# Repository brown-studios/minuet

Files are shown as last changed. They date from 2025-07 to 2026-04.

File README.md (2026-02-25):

# Minuet fan controller

Minuet upgrades your [MAXXAIR Maxxfan](https://www.maxxair.com/products/fans/maxxfan-deluxe/) with a brushless DC motor, home automation features, and accessories.

Improve your quality of life in your campervan, RV, trailer, or truck!

* Replace your fan's original motor with a quieter brushless motor. No more cleaning squeaky motor brushes!
* Install Minuet with simple hand tools. You can revert back to the original equipment later if you want.
* Connect your fan to your home automation system if you have one. Works with your original infrared remote control and wired wall controls too.
* Install the light accessory to add a ring of lights to your fan for illumination and ambiance.
* Install the cover sensor accessory to stop the fan and turn off the lights automatically when you attach an insulated vent cover.
* Enjoy a more polished user experience with enhanced thermostat controls and less beeping.
* Customize your fan as you like because the firmware and hardware are open source!
  * Expand the [ESPHome](https://esphome.io/)-based [firmware](https://github.com/brown-studios/minuet-firmware).
  * Connect off-the-shelf I2C environmental sensors and devices to the [QWIIC](https://www.sparkfun.com/qwiic) port.
  * Make your own hardware accessories for the expansion port.
  * Share your work with the community!

This repository contains the Minuet documentation and hardware design files.  You are welcome to modify the Minuet firmware and hardware subject to the [license terms](#notice) and we encourage you to make your own accessories.  We welcome thoughtful contributions.

*Refer to the [Minuet firmware repository](https://github.com/brown-studios/minuet-firmware) for source code.*

## Get to know Minuet

Watch Minuet in action and follow along with how it was made with these videos:

* [Minuet showcase](https://vimeo.com/showcase/11857354)
* [Minuet build log](https://vimeo.com/showcase/11858950)

## Project status

Minuet is in active development.

The latest prototype is feature complete, works well, and is being tested by a few volunteers.

Our next tasks are finalizing the design, working with manufacturers to fabricate kits with everything you will need to upgrade your Maxxfan, and planning for order fulfillment.  We are also investigating the possibility of manufacturing custom brushless fan motors that will fit into the fan housing with fewer adapters.  Please contact us if you would like to contribute your manufacturing experience to this project.

Watch this space for updates on our progress.  We're thrilled by your interest in Minuet and we look forward to offering you a great upgrade for your Maxxfan!

See [project history](./docs/project-history.md) for the story of how we got here.

## Author's note

Hey folks, I'm Jeff!

I started building my campervan in 2023 after some delightful adventures in New Zealand.  Like many of you, I installed a Maxxfan in my campervan because it was the most popular fan for van builders.  It worked well for a while but less than a year after I installed it, the fan started making some awful squeaking noises.  I tried the usual advice: clean the motor brushes, replace the bearings, run the motor on high for a day, and nothing helped for long.  I tried to ignore the problem.

When the winter rainy season arrived and interrupted my van build, I started the squeaking fan again.  I had already started designing a circuit board to synchronize the Maxxfan with my home automation system and I found it tedious to work around the existing logic of the Maxxfan circuit board.  It occurred to me that it might be easier to design my own controller from scratch... and then I could use a brushless fan motor and solve my fan squeaking problem too!

So here we are.  I've made several prototypes, enjoyed the quiet, added quality of life features, made some friends, and learned a lot along the way.  I'm satisfied with how Minuet has improved my comfort and I hope you'll like it too.

## Getting started

Read these guides to learn how to build, install, and use Minuet and its accessories.

1. [Hardware guide](docs/hardware-guide.md): How to build Minuet hardware.
1. [Installation guide](docs/installation-guide.md): How to install Minuet into your Maxxfan.
1. [User guide](docs/user-guide.md): How to use Minuet.

Good luck and enjoy your fan!

## Compatibility

Minuet is anticipated to be *compatible* with the following Maxxfan models.  Some models have yet to be specifically tested and are shown as unverified in the table.

| Compatible model | Lid type | Lid color | Temperature sensor | Rain sensor | Infrared receiver | Verified |
| --- | --- | --- | --- | --- | --- | --- |
| Maxxfan Deluxe 7500K | rain cover | smoke | yes | no | yes | yes |
| Maxxfan Deluxe 7000K | rain cover | white | yes | no | yes | no |
| Maxxfan Deluxe 6200K | rain cover | smoke | yes | no | no † | no |
| Maxxfan Deluxe 5100K | rain cover | white | yes | no | no † | no |
| Maxxfan Plus 4500K‡ | low profile | smoke | yes | yes | yes | yes |

†: When you install Minuet in a Maxxfan whose keypad does not have a window for an infrared receiver, you will be unable to use Minuet's infrared remote control features. (It may be possible to replace or punch a hole through the keypad to make a window for the infrared receiver and use its features.)

‡: The Maxxfan Plus 4500K lid takes longer to open and close so the firmware must be modified to account for the extra duration as of Minuet v3.0.  This difference will be resolved by improving end-of-travel detection.

Minuet is *not compatible* with the following Maxxfan models.

| Incompatible models | Reason |
| --- | --- |
| Maxxfan Deluxe 5101K, 6201K, 7001K, 7501K, 8001K, 8501K | exhaust only keypad (no in/out button) |
| Maxxfan Deluxe 5301K, 6401K | 4 speed keypad (different buttons) |
| Maxxfan Plus 4000K, 4002K, 4050K | manual lift |
| Maxxfan 4301K, 4401K, 4501K | manual lift |
| Maxxfan Low Profile, Mini, Dome | different electronics |

## Notice

The Minuet software, documentation, design, and all copyright protected artifacts are released under the terms of the [MIT license](LICENSE).

The Minuet hardware is released under the terms of the [CERN-OHL-W license](hardware/LICENSE).

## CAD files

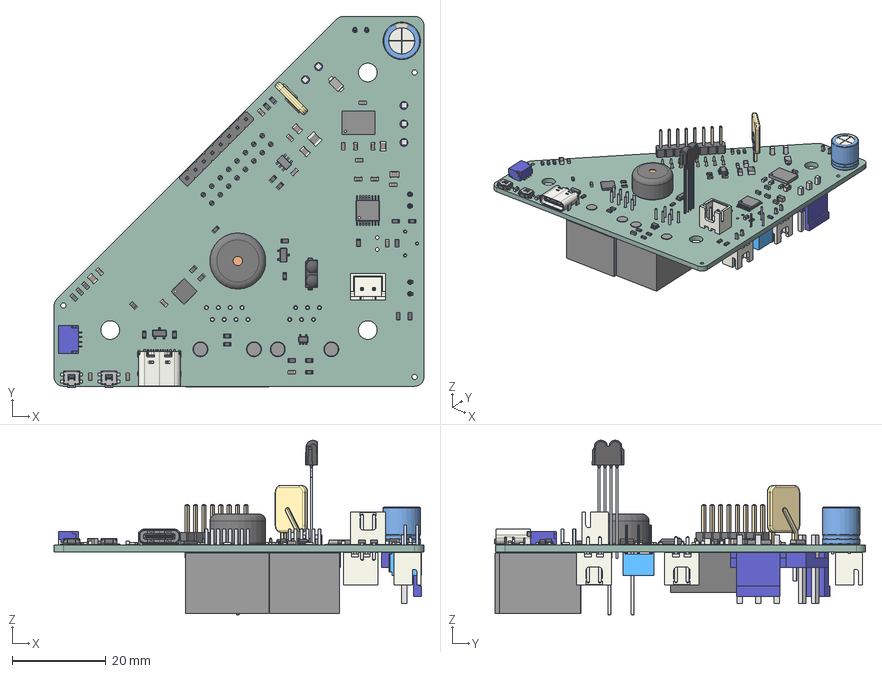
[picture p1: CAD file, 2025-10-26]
hardware/minuet/v4/minuet.step
79.0 x 79.3 x 37.3 mm
C_0805_2012Metric x 5
L_1008_2520Metric
D_SMF
R_0603_1608Metric x 26
C_0603_1608Metric x 17
TPS561201
CP_Radial_D8.0mm_P3.50mm
GO-100220.31
GO-100220.1_Rev01
DRV8876PWPR
SOT-23 x 2
SM04B-SRSS-TB
SW_SPST_EVQP7A x 2
SOT-353_SC-70-5
RGEF400
USB_C_Receptacle_GCT_USB4105-xx-A_16P_TopMnt_Horizontal
Texas_RTW_WQFN-24-1EP_4x4mm_P0.5mm_EP2.7x2.7mm
MCF8316D
Buzzer_TDK_PS1240P02BT_D12.2mm_H6.5mm
PinHeader_1x08_P2.54mm_Vertical
JST_XH_B2B-XH-A_1x02_P2.50mm_Vertical x 4
3362P-1-502LF
Lugs x 2
Leads x 2
B2P-VH-B
PinSocket_2x08_P2.54mm_Vertical
B3P-VH-B
minuet_PCB

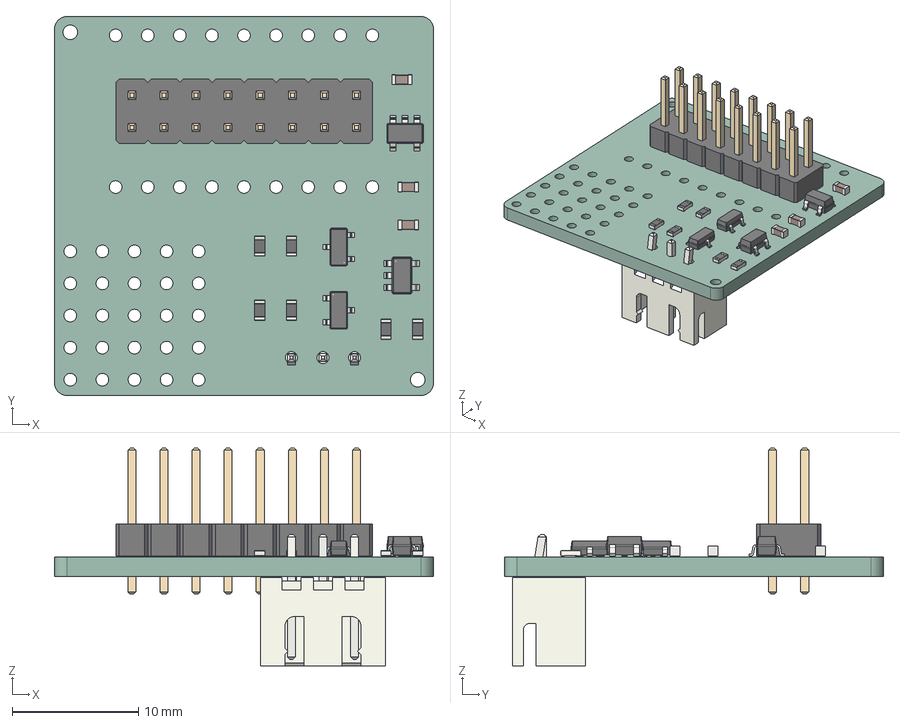
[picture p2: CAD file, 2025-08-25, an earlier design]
hardware/light/v3/light.step
30.0 x 30.0 x 17.2 mm
SOT-23 x 2
PinHeader_2x08_P2.54mm_Vertical
R_0603_1608Metric x 6
SOT-23-5 x 2
C_0603_1608Metric x 3
JST_XH_B3B-XH-A_1x03_P2.50mm_Vertical
light_PCB

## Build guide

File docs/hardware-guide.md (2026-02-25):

# Minuet hardware guide

This guide explains how to build Minuet hardware.

- [Project organization](#project-organization)
- [Main parts](#main-parts)
  - [Fan controller](#fan-controller)
  - [Fan motor and adapters](#fan-motor-and-adapters)
  - [Power cable](#power-cable)
  - [Lid motor cable](#lid-motor-cable)
- [Accessories](#accessories)
  - [Light accessory](#light-accessory)
  - [Cover sensor accessory](#cover-sensor-accessory)
  - [Making your own accessories](#making-your-own-accessories)

> [!TIP]
> Consider buying a Minuet kit when they become available to save yourself time and money.  And read on to learn about the hardware!

# Project organization

## Circuit board designs

The [hardware](../hardware/) folder contains all of the Minuet circuit board designs.

Each circuit board major revision resides in its own subfolder and includes a KiCad project, design document with errata, PDF plot of the schematics, and 3D renderings.  Refer to the `design-and-errata.md` for each circuit board to learn how it's supposed work, how the design has evolved through each minor revision, what was learned from that revision, and workarounds for known issues.

- [Minuet v3 design and errata](../hardware/minuet/v3/design-and-errata.md)
- [Light accessory v3 design and errata](../hardware/light/v3/design-and-errata.md)

## Fabricating circuit boards

Refer to each circuit board's design document for specific fabrication notes.

This repository does not contain fabrication files; you can generate them from the KiCad project in whatever format you need.

The KiCad projects contain part numbers and placement information for the JLCPCB PCBA service.  Use the [Fabrication Toolkit](https://github.com/bennymeg/Fabrication-Toolkit) plugin for KiCad to generate the fabrication files for JLCPCB including the gerber files, bill of materials, and part positions.  Many of the parts in the design were selected to reduce fabrication cost at JLCPCB.  At the time of this writing, the MCF8316D motor driver chip had to be sourced from the global supply chain because was not a regularly stocked item at JLCPCB.

If you're using a different PCBA service, you'll need to select equivalent parts.

Some of the SMT parts have fine pitch QFN pads that are not accessible to a soldering iron.  You may need a solder stencil and reflow equipment to assemble these parts reliably.

You may find it more cost effective to have the factory assemble front-side SMT and through-hole parts and then install the remaining back-side through-hole parts by hand.

## Circuit board design guidelines

Here are a few guidelines to consider when contributing to the Minuet circuit board designs:

- Do not check in fabrication files because they're hard to keep in sync with the design files.
- Include links to datasheets for each chip in the KiCad symbols.
- Prefer two-layer boards to keep the designs accessible for hobbyists.
- Prefer SMT parts no smaller than 0603 and keep the layout somewhat sparse to facilitate hand assembly.
- Place SMT parts on the front side of the board only.
- Place through-hole parts on either side as needed for mechanical reasons.
- Place prominent silk screen labels next to each connector and reference it in the documentation.
- Assign net classes to nets that carry high current.
- Record errata in the design document.

## KiCad resources

To edit the hardware projects, you will need the following:

- KiCad version 9.0 or newer
- KiCad add-ons installed using the Plugin and content manager
  - [Espressif Library](https://github.com/espressif/kicad-libraries): symbols and footprints
  - [JLCPCB Fabrication Toolkit](https://github.com/bennymeg/Fabrication-Toolkit): exports files for manufacturing

# Main parts

## Fan controller

The Minuet fan controller circuit board drives the show.

It is a drop-in replacement for the original Maxxfan circuit board with the original fasteners in the same screw positions and it supports all of the built-in Maxxfan hardware (except the fan motor because that's been replaced by a brushless motor).  Of course, it can do a whole lot more in the same space!

This circuit board has special assembly instructions for the infrared receiver and for adjusting the lid motor current limit trim potentiomer.

Circuit board details: [Minuet v3 design and errata](../hardware/minuet/v3/design-and-errata.md)

Once you've fabricated the circuit board, install the [Minuet firmware](https://github.com/brown-studios/minuet-firmware).

## Fan motor and adapters

Minuet uses a brushless DC motor to drive the fan instead of the original brushed DC motor.

Here's how to choose a fan motor and make adapters to fit the motor to the fan housing.  We recommend choosing a known compatible motor if possible because the process for tuning motors is somewhat challenging.

### Compatible motors

#### StepperOnline 57BYA54-12-01 ([supplier](https://www.omc-stepperonline.com/12v-3000rpm-0-16nm-50w-5-90a-57x57x53-5mm-brushless-dc-motor-57bya54-12-01))

**This is the only motor currently supported out-of-the-box by Minuet.**

- Runs quietly and continuously from about 100 RPM to over 1200 RPM.
- Readily available, compact, and inexpensive.
- Needs a shaft adapter to extend the shaft to reach the fan blade.
- Needs a mount adapter to compensate for the screw hole locations.
- The hall sensors are not needed and are not used by Minuet.

##### Specifications

- Rated voltage: 12 V
- Rated power: 50 W
- Rated current: 5.9 A
- Motor poles: 4
- Sensor type: 3 digital hall sensors with 30° placement
- Shaft diameter: 8 mm
- Shaft length: 21 mm
- Fastener: 4x M4 screws
- Dimensions: 57 mm diameter x 53.5 mm length

##### Wiring chart

- Phase A: fat yellow wire
- Phase B: fat green wire
- Phase C: fat blue wire
- The remaining wires are for the unused hall sensor and can be secured out of the way or cut off

### Bringing up other motors

#### Motor selection guide

Choose a motor that runs quietly at low speed with minimum vibration.  It doesn't need a lot of torque.  For safety, it must be able to operate continously under load without overheating.  Look for motors that are designed for use in appliances (not for skateboards or model airplanes).

The motor must be brushless.  The 3 phases can be wired in either the wye or delta configuration.

The motor should have a datasheet with published specifications so you know what you're getting.

The motor should have a suitable power rating, perhaps somewhere around 50 W, certainly not hundreds of watts.  Bigger is not better.  Big motors have big magnets and they experience significant [cogging torque](https://en.wikipedia.org/wiki/Cogging_torque) when operated at low speeds which results in excessive noise and vibration for a vent fan.

The motor should be designed for operation at a nominal 12 V.  The actual operating voltage will depend on the supply voltage.

The motor should have a minimum current rating of 4 A per phase.  You can use a smaller motor with a lower current rating but it may not be powerful enough to operate the fan at higher speeds.

The motor should not have hall sensors.  It's ok to have them but Minuet v3 does not use them (previous versions of Minuet did).

You are unlikely to find a suitable motor that is a perfect drop-in replacement for the original motor's dimensions.  That's just physics.  Brushless DC motors are generally more efficient than brushed DC motors of equivalent power so they tend to be smaller.  So you will likely need to make adapters to compensate for the different motor body size, mounting hole pattern, shaft diameter, shaft length, and shaft keying.

#### Motor tuning

Before you can operate a new motor with Minuet, you will need to add the motor to a [table in the Minuet firmware](https://github.com/brown-studios/minuet-firmware/blob/main/minuet/fan_driver.h) and tune a large number of parameters for the [MCF8316D field-oriented control motor driver chip](https://www.ti.com/lit/ds/symlink/mcf8316d.pdf).

Those parameters include:

- Number of poles
- Winding resistance
- Winding inductance
- Back-EMF constant
- Speed control loop terms
- Current limit
- Open loop and closed loop acceleration
- Initial position detection
- Operating speed table

Some of these parameters can be measured or estimated directly by the motor driver chip using the built-in Motor Parameter Extraction Tool.  Other parameters require experimentation to determine optimal values for reliable operation.  It is helpful to have a TI MCF8316D-EVM development board and the TI Motor Studio software.

If the motor spins the wrong direction (e.g. intake when it should be exhaust), swap any two motor phases and record that in your wiring chart.

Explaining the process of motor tuning in detail is beyond the scope of this guide.

### Motor wiring

Here's how to attach a connector to your fan motor if it doesn't already have one that's compatible with Minuet.

##### Supplies

- [JST VH series wire-to-board connectors](https://www.jst.com/products/crimp-style-connectors-wire-to-board-type/vh-connector/)
  - 1x JST VH series VHR-3M housing
  - 3x JST VH series SVH-41T-P1.1 contacts plus a few spares just in case
  - If your wires are too short (see instructions)
    - 18 AWG wire, heat shrink tubing, and soldering supplies
  - A crimping tool

##### Instructions

- Locate the wiring chart for your motor and note the color of the A, B, and C phases.
- Measure your wires.  The wires need to be about 16-20" or 40-50 cm long to comfortably reach from the motor to the circuit board within the fan housing.  If your wires are too short then you can solder on some additional 18 AWG wire.
- Strip the wires back about 1.5 mm.
- Crimp the pins onto each wire.
- Note the numbers or index markings on the side of the connector housings to determine the pin order.
- Assemble the 3-pin motor connector as follows:
  - pin 1: Phase A
  - pin 2: Phase B
  - pin 3: Phase C
- Give the wires a gentle tug to ensure they have been fully seated and latched into the housing.

### Motor shaft adapter

The original fan motor has a 40 mm long, 8 mm diameter D-shaped shaft, with a flat face on one side where the fan blade attaches with a 26 mm deep hub.  Your motor's shaft is probably different so you will need a shaft adapter to achieve the necessary length and diameter.

Here are some ways to assemble a suitable shaft adapter.

#### Rigid coupler and dowel pin shaft adapter

This adapter consists of two parts, a rigid coupler to match the shaft diameter and an 8 mm dowel pin to extend its length to fit the fan blade.

TODO: Add a photo

##### Supplies

- Rigid coupler.  The inner diameter of one end of the coupler must match the diameter of your motor shaft and the other end must be 8 mm to match the dowel pin.
  - [5 mm to 8 mm inner diameter, 22 mm long stainless steel coupler](https://www.amazon.com/gp/product/B07P82D36N/)
  - [8 mm to 8 mm inner diameter, 22 mm long stainless steel coupler](https://www.amazon.com/gp/product/B07P5YZKY5/)
- Dowel pin.  The exposed length of the dowel pin must be at least 26 mm for the fan blade plus enough to insert into the shaft coupler.  A dowel pin with 40 mm overall length works well with the couplers linked above.
  - [8 mm x 40 mm stainless steel dowel pin](https://www.amazon.com/gp/product/B07Z6GC2TR/)

##### Instructions

1. Optional: File a shallow flat face into one end of the dowel pin about 15 mm long.  The flat face helps to prevent the fan blade's grub screw from slipping on the shaft although it doesn't seem to make much difference so you can skip this step.
1. Seat the 8 mm dowel pin up to the midpoint of the coupler such that about 26 to 30 mm of the shaft (flattened end) sticks out.  Gently tighten the coupler's grub screws onto the dowel pin.
1. Insert the coupler onto the motor shaft.  Gently tighten the coupler's grub screws onto the dowel pin.

#### 3D printed shaft adapter

Here's a [model for a 3D printed shaft adapter](https://cad.onshape.com/documents/c87749ce3cf87a164617aa11/w/1134a70d634f5c16dbb7ae0d/e/bb8abe1ffa8084825e8f7efa).  You can configure the model for whatever motor shaft diameter you need.  Attach the adapter to the motor shaft with a pair of M4 grub screws.

**Safety notice**: The shaft adapter experiences significant torque while running the fan so there's a risk it might break or slip off the shaft and hurt someone.  Consider making a shaft adapter from more robust materials.  Please be careful!

TODO: Add a photo

### Motor mount

You will need a mount to securely attach your new fan motor to the Maxxfan's housing which was originally designed for a motor with different dimensions.

The mount has three essential features:

- Two M5 screws spaced 50 mm apart across the diameter of the motor for mounting the motor to the housing, just like the original motor.
- Screw holes for fastening the new motor to the mount.
- Spacers to backset the new motor from the housing to compensate for the excess length of the shaft adapter so the fan blade fits properly.  Without them, the fan blade will stick out too far to fit behind the insect screen.

Here are some ways to assemble a suitable mount.

#### 3D printed mount

Here's a [configurable model](https://cad.onshape.com/documents/11f07c0bb608e7010778ac35/w/a82f75dceda39e564795dbd4/e/9979bb27f5cf3d9f46ddfa29) that you can use as a starting point.  It has integrated spacers and stiffening ribs to backset the motor so the shaft sticks out just the right amount for the fan blade to attach.

Use a strong plastic with good heat and UV resistance such as PETG.

TODO: Add a photo

##### Supplies

- 2x M5 x 14 mm cap screws (a little longer is ok) and washers
- Screws for your motor and shaft adapter combination
  - For 57BYA54 with a rigid coupler and dowel pin shaft adapter, use 4x M4 x 22 mm socket head cap screws and washers

##### Instructions

1. Tap the M5 screw holes into the plate.
1. Screw the M5 screws through the mount from the side on which the motor is installed.  Tighten only until snug to avoid stripping the plastic threads.  Do not use threadlocker.
1. Screw the motor to the plate.  Add a washer on each screw between the screw head and the plate.

### Wire passage cover

The notch in the original wire passage cover is too small to fit over the motor wires.

You can modify the original wire passage cover to fit, make a new cover, or omit the cover (increasing the risk of water intrusion).

#### 3D printed cover

Here's a [configurable model](https://cad.onshape.com/documents/c87749ce3cf87a164617aa11/w/1134a70d634f5c16dbb7ae0d/e/c150dd1f03cfafd0dbefc852) that you can use as a starting point.

Use a strong plastic with good heat and UV resistance such as PETG.

TODO: Add a photo

## Power cable

The power cable uses a [JST VH series wire-to-board connector](https://www.jst.com/products/crimp-style-connectors-wire-to-board-type/vh-connector/).

- Pin 1 is negative (ground)
- Pin 2 is positive (+12 V DC nominal)

TODO: Add a photo

##### Supplies

- 1x JST VH series VHR-2M housing
- 2x JST VH series SVH-41T-P1.1 contacts plus a few spares just in case
- 18 AWG wire, preferably in distinct colors to help identify positive (red) and negative (black)
- wire crimping tools

##### Instructions

- Cut two pieces of wire long enough to make the connection from the fan housing where the circuit board will be installed to the electrical supply.  About 12" or 30 cm should be plenty.  Alternatively, you can crimp the contacts directly to the electrical supply wire.
- Strip 2 mm off the end of the wire.
- Crimp the JST VH contacts to the wires.
- Insert the contacts into the JST VH housing paying attention to the polarity chart shown above.

## Lid motor cable

This cable adapts the lid motor's [Molex 1625 series wire-to-wire connector](https://www.molex.com/en-us/products/series-chart/1625) to Minuet's [JST XH series wire-to-board connector](https://www.jst.com/products/crimp-style-connectors-wire-to-board-type/xh-connector/).

TODO: Add a photo

##### Supplies

- 1x Molex 1625 series 03061023 (1625-2R3) receptacle
- 2x Molex 1625 series 02061101 contacts plus a few spares just in case
- 1x JST XH series XHP-2 2-pin housing
- 2x JST XH series SXH-001T-P0.6(N) contacts plus a few spares just in case
- 22 AWG 2 conductor ribbon cable
- wire crimping tools

##### Instructions

- Cut a section of ribbon cable approximately 12" or 30 cm long.
- Strip 1.5 mm off from each end of each wire.
- Crimp a Molex 1625 series pin to one of each wire and a JST XH series pin to the other end.
- Insert the pins into their respective housings such that pin 1 of the Molex 1625 series connector connects to pin 1 of the JST XH series connector.  Likewise, pin 2 connects to pin 2.

# Accessories

## Light accessory

The Minuet light accessory lets you attach a light to your fan.  It plugs into the Minuet `EXPANSION` port.

You can use this accessory as a break-out board for your own circuits and it includes a prototyping area for mounting through-hole components.

Circuit board details: [Minuet light accessory v3 design and errata](../hardware/light/v3/design-and-errata.md)

### LED strip

This section section describes how to build an addressable LED strip with a connector that works with Minuet out-of-the-box.  You can use a different LED strip instead but you may need to customize the firmware to interface with it correctly.

TODO: Add a photo

##### Supplies

- 1 meter of [BTF Lighting SK6812 RGBWW, IP65, 60 LEDs/meter, 12 V](https://www.btf-lighting.com/products/dc12v-sk6812-rgbw-led-strip-individual-addressable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) or similar
- 1x JST XH series XHP-3 3-pin housing
- 3x JST XH series SXH-001T-P0.6(N) contacts plus a few spares just in case
- 22 AWG 3 conductor ribbon cable
- wire crimping tools
- heat shrink tubing

##### Instructions

- Cut a section of ribbon cable approximately 12" or 30 cm long.
- Cut a section of 57 pixels from the LED strip.  This is enough to fit around the inner circumference of the fan housing.
- Solder one end of each wire to the `GND`, `DIN`, and `12V` terminals of the LED strip.
- Install a short section of heat shrink tubing over the solder joint.
- Strip 1.5 mm off from the other end of each wire.
- Crimp a JST XH series pin to one end of each wire.
- Insert the pins into the JST XH series housing such that pin 1 connects to `GND`, pin 2 connects to `DIN`, and pin 3 connects to `12V`.

## Cover sensor accessory

The cover sensor accessory detects when you have installed an insulated vent cover and engages the safety lock to turn off the fan and the light.

It's a normally-open reed switch that plugs into the `LOCK` connector.  The reed switch closes the circuit when a magnet on the cover is adjacent to it.

TODO: Add a photo

##### Supplies

- 1x normally-open reed switch with axial leads, such as [this one](https://www.amazon.com/dp/B07YFBQ4HS)
- 1x JST XH series XHP-2 2-pin housing
- 2x JST XH series SXH-001T-P0.6(N) contacts plus a few spares just in case
- 22 AWG 2 conductor ribbon cable
- wire crimping tools
- heat shrink tubing

##### Instructions

- Cut a section of ribbon cable approximately 24-30" or 60-75 cm long.  It needs to be long enough to reach from the fan controller to the fan ceiling flange where it can sense the magnet on the cover.
- Bend one lead of the reed switch over so that both leads point the same direction.
- Solder one end of each wire to each lead of the reed switch.  To keep things tidy, it helps to trim the wire and the leads so they lay flat before soldering.
- Install a section of heat shrink tubing over the reed switch and its leads.
- Strip 1.5 mm off from the other end of each wire.
- Crimp a JST XH series pin to one end of each wire.
- Insert the pins into the JST XH series housing.  The pin order doesn't matter.

## Making your own accessories

Minuet gets better when you take advantage of its place in the middle of your vehicle's roof for accessories.

- Attach many off-the-shelf [QWIIC](https://www.sparkfun.com/qwiic) compatible I2C peripherals to Minuet with just a wire.
- Use the [Light accessory](#light-accessory) as a break-out board for your own circuits and it includes a prototyping area for mounting through-hole components.
- Make your own circuit board that plugs into the `EXPANSION` port.

Refer to the [Minuet v3 design and errata](../hardware/minuet/v3/design-and-errata.md) and schematics for the electrical parameters of these ports.

> [!TIP]
> You will likely need to customize the [Minuet firmware](https://github.com/brown-studios/minuet-firmware) for your accessory.  We recommend consulting the list of [ESPHome components](https://esphome.io/components/) to help choose your peripherals so you won't need to write as much code to get them working.

Here are some ideas of stuff you could build:

- Add a CO₂, temperature, humidity sensor: [scd4x sensor](https://esphome.io/components/sensor/scd4x.html)
- Add a temperature, pressure sensor, humidity, gas sensor: [bmp680 sensor](https://esphome.io/components/sensor/bme680)
- Add a button near the fan to trigger something: [gpio binary sensor](https://esphome.io/components/binary_sensor/gpio)
- Add a relay to do something when the fan is running: [gpio switch](https://esphome.io/components/switch/gpio)
- Detect when humans are present: [dfrobot sen0395](https://esphome.io/components/dfrobot_sen0395)

Consider sharing your new accessory with others! ❤️

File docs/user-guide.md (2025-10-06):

# Minuet user guide

This guide explains how to use Minuet.

- [Main functions](#main-functions)
- [Light accessory functions](#light-accessory-functions)
- [WiFi network](#wifi-network)
- [Automation](#automation)
- [Minuet app (help wanted)](#minuet-app-help-wanted)

# Main functions

You can control most of the fan's functions using the built-in keypad.  Some functions can only be used when you have certain accessories installed or using automation (see related sections).

## Using the built-in keypad and the 6 key wall remote

Minuet supports two different control schemes for the built-in keypad and the 6 key wall remote.  After all, why not improve on the fan controls when you're already replacing its brains!

The [enhanced controls](#enhanced-controls) are enabled by default and make the automatic thermostat easier to use and more capable.

If you prefer, you can enable the [standard controls](#standard-controls) instead to mimic the original Maxxfan controls with some loss of functionality.

### Quick reference

These button combinations vary by control mode.

| Button combination | Enhanced controls | Standard controls (manual mode) | Standard controls (auto mode) |
| --- | --- | --- | --- |
| press `up` | speed up | speed up | thermostat temperature up |
| hold `up` for 1 second | speed maximum | speed maximum | |
| press `down` | speed down | speed down | thermostat temperature down |
| hold `down` for 1 second | speed minimum | speed mimimum | |
| press `in/out` | direction in/out | direction in/out | direction in/out |
| press `on/off` | fan on/off | fan on/off | thermostat disable (return to manual mode) |
| press `open/close` | lid open/close | lid open/close | |
| press `auto` | thermostat enable/disable | thermostat enable (enter auto mode) | thermostat disable (return to manual mode) |
| hold `auto` for 3 seconds | thermostat reset | | thermostat reset |
| hold `auto` and press `up` | thermostat temperature up | | |
| hold `auto` and press `down` | thermostat temperature down | | |
| hold `auto` and press `in/out` | thermostat direction toggle | | |
| hold `auto` and press `on/off` | thermostat function toggle | | |

These button combinations are common to all modes.

| Button combination | Behavior |
| --- | --- |
| press `rain` | rain sensor toggle (only for models with rain sensors) |
| hold `auto` and `up` for 5 seconds | use enhanced controls |
| hold `auto` and `down` for 5 seconds | use standard controls |
| hold `auto` and `open/close` for 5 seconds | keypad indicator toggle |
| hold `on/off` and `in/out` for 5 seconds | manual safety lock toggle |
| hold `on/off` and `down` for 5 seconds | WiFi toggle |
| hold `on/off` and `up` for 5 seconds | power on restore toggle |
| hold `on/off` for 15 seconds | factory reset |

These button combinations are available when you have the corresponding accessory installed.

| Button combination | Light accessory |
| --- | --- |
| hold `in/out` for 1 second | light on/off |
| hold `in/out` for press `up` | brightness up |
| hold `in/out` for press `down` | brightness down |

### Enhanced controls

The enhanced controls let you keep the automatic thermostat enabled while you manually override its behavior for particular situations like when you need extra ventilation for cooking indoors.  The buttons always behave the same way regardless of whether the thermostat is enabled.

While the thermostat is disabled, the `auto` indicator is unlit and the buttons control the fan state similar to the standard controls.

While the thermostat is enabled, the `auto` indicator is lit and the thermostat controls the fan state automatically based on the ambient temperature.  However, if you press a button or send an automation request to change the state of the fan with enhanced controls then your manual settings *override* the behavior of the thermostat.  This behavior differs from the [standard controls](#standard-controls) where such changes are disallowed unless the thermostat is disabled.

While the thermostat is overridden, the `auto` indicator blinks and the buttons control the fan state similar to the standard controls.  The thermostat will remain overridden state by your manual settings until you press `auto` to re-engage the thermostat.

Hold `auto` and press other buttons to modify the thermostat temperature set point, direction, and function with the keypad.  Use the [automation](#automation) interfaces to configure more advanced features of the thermostat.

*To enable the enhanced controls, press and hold `auto` and `up` simultaneously for 5 seconds.  Minuet confirms with three quick tones followed by a long high tone.*

#### Buttons

- Press `up`: increase the fan speed by one
- Hold `up` for 1 second: increase the fan speed to maximum *(bonus)*
- Press `down`: decrease the fan speed by one
- Hold `down` for 1 second: decrease the fan speed to minimum *(bonus)*
- Press `in/out`: toggle the fan direction between air in and air out
- Press `on/off`: toggle the fan off or turn it on at its last selected manual fan speed
- Press `open/close` (`up` and `down` together): toggle the lid open or closed
- Press `auto`: enable the thermostat if it is disabled, re-engage the thermostat if it is overridden, otherwise disable the thermostat
- Hold `auto` for 3 seconds: reset thermostat to default temperature setpoint of 78 °F (approx. 25.5 °C), default direction, and default function, Minuet confirms with a quick turn
- Hold `auto` and press `up`: increase thermostat temperature setpoint by 1 °F (approx. 0.5 °C), Minuet confirms with a quick rising tone
- Hold `auto` and press `down`: decrease thermostat temperature setpoint by 1 °F (approx. 0.5 °C), Minuet confirms with a quick falling tone
- Hold `auto` and press `in/out` one or more times: set the thermostat direction according to the number of presses of `in/out` as indicated in the *thermostat direction* table

  | Thermostat direction | Key presses | Behavior | Confirmation |
  | -------------------- | ----------- | -------- | ------------ |
  | *default* | 1 | use the last selected manual fan direction | two quick tones |
  | *air out* | 2 | exhaust air from the vehicle | quick rising scale |
  | *air in* | 3 | draw air into the vehicle | quick descending scale |

- Hold `auto` and press `on/off` one or more times: set the thermostat function according to the number of presses of `on/off` as indicated in the *thermostat function* table

  | Thermostat function | Key presses | Fan mode | Lid mode | Behavior | Confirmation |
  | ------------------- | ----------- | -------- | -------- | -------- | ------------ |
  | *default* | 1 | fan auto | lid auto | **best for cooling**: automatic fan speed control | long tone, quick tone |
  | *quiet* | 2 | fan quiet | lid open | **best for sleeping**: quieter automatic fan speed control, lid stays open even below the temperature setpoint to provide fresh air and eliminate actuator noises (unless overridden by a safety lock) | long tone, two quick tones |
  | *low* | 3 | fan low | lid auto | **best for energy efficiency**: fan speed at minimum | long tone, three quick tones |
  | *passive* | 4 | fan off | lid auto | **best for passive ventilation**: fan stays off | long tone, four quick tones |

### Standard controls

The standard controls mimic the original Maxxfan controls with a few *bonus* convenience features.

The buttons behave differently depending on whether the fan is in manual or in auto mode.  Check the state of the `auto` indicator light before pressing buttons to avoid surprises.  For example, in manual mode the `up` and `down` buttons control the fan speed whereas in auto mode the `up` and `down` buttons control the thermostat temperature setpoint.

If Minuet receives an automation request to change the fan speed or open/close the lid while auto mode is active with standard controls, it returns to manual mode before performing the requested action.  This behavior differs from the [enhanced controls](#enhanced-controls) where such changes are allowed and override the behavior of the thermostat.

*To enable the standard controls, press and hold `auto` and `down` simultaneously for 5 seconds.  Minuet confirms with three quick tones followed by a long low tone.*

#### Buttons in manual mode (`auto` indicator is unlit)

In manual mode, the up/down buttons control the fan speed and the on/off button toggles the fan on or off.

- Press `up`: increase the fan speed by one
- Hold `up` for 1 second: increase the fan speed to maximum *(bonus)*
- Press `down`: decrease the fan speed by one
- Hold `down` for 1 second: decrease the fan speed to minimum *(bonus)*
- Press `in/out`: toggle the fan direction between air in and air out
- Press `on/off`: toggle the fan off or turn it on at its last configured manual fan speed
- Press `open/close` (`up` and `down` together): toggle the lid open or closed
- Press `auto`: enable the thermostat, enter auto mode

#### Buttons in auto mode (`auto` indicator is lit)

In auto mode, the up/down buttons control the thermostat temperature setpoint, the on/off button exits auto mode, and the thermostat controls the fan speed based on the ambient temperature.  The thermostat will turn the fan on in the direction it last operated in.

- Press `up`: increase thermostat temperature setpoint by 1 °F (approx. 0.5 °C), Minuet confirms with a quick rising tone
- Press `down`: decrease thermostat temperature setpoint by 1 °F (approx. 0.5 °C), Minuet confirms with a quick falling tone
- Press `in/out`: toggle the fan direction between air in and air out
- Press `on/off`: disable the thermostat, return to manual mode
- Press `open/close` (`up` and `down` together): *inoperable in this mode*
- Press `auto`: disable the thermostat, return to manual mode
- Hold `auto` for 3 seconds: reset thermostat to default temperature setpoint of 78 °F (approx. 25.5 °C), Minuet confirms with a quick turn

### Rain sensor (only for models with rain sensors)

Press the `rain sensor` button to toggle the rain sensor on or off.

When the rain sensor is disabled, the LED will turn red to warn that water could enter your vehicle if it rains.

When the rain sensor detects moisture, it turns off the fan, closes the lid, makes the LED flash red, and activates the safety lock feature.  The fan cannot be operated while the safety lock is activated.  Press the `rain sensor` button again to reset the flashing LED and release the rain sensor safety lock.

### Safety lock

The safety lock feature closes the lid and prevents the fan from being operated whenever one or more of the following conditions occur:

| Reason | Condition | How to release |
| --- | --- | --- |
| Battery safety lock | The battery voltage is too low to too high. | Wait for the battery voltage to return to the normal operating range or adjust the low or high battery voltage thresholds. |
| Rain safety lock | The rain sensor is enabled and detected moisture. | Press the `rain sensor` button to reset or turn off the rain sensor. |
| Accessory safety lock | An accessory triggered the `LOCK` signal. | Consult the documentation of your accessories for details. For example, if you have a sensor to detect the presence of an insulated vent cover then remove the cover. |
| Manual safety lock | The [manual safety lock](#manual-safety-lock) is enabled. | Disable the [manual safety lock](#manual-safety-lock). |
| Automation safety lock | The [automation safety lock](#automation-safety-lock) is enabled. | Disable the [automation safety lock](#automation-safety-lock). |

You cannot turn the fan on or open the lid while the safety lock is active.  If you try, Minuet plays three quick tones as a warning and rejects the request.

The safety lock also turns off and inhibits the light accessory.

#### Manual safety lock

Use the manual safety lock to keep the fan off and the lid closed to prevent the fan from operating accidentally or under control of the thermostat.  For example, it can be helpful to keep out dust and wildfire smoke in extreme conditions or perhaps to discourage an inappropriately inquisitive child from turning on the fan.

Hold `on/off` and `in/out` together for 5 seconds to toggle the manual safety lock.  By default, the manual safety lock is disabled.

When the manual safety lock is enabled, Minuet confirms with two quick tones followed by a long high tone.

When the manual safety lock is disabled (default), Minuet confirms with two quick tones followed by a long low tone.

#### Automation safety lock

Use the automation safety lock to develop automations that keep the fan off and the lid closed under software defined conditions.  Unlike [manual safety lock](#manual-safety-lock), the automation safety lock cannot be toggled using the keypad; it can only be toggled by automations.

For example, you could write an automation to enable the automation safety lock while driving (to reduce road noise and fumes) and disable it when parked.

### WiFi mode

Hold `on/off` and `down` together for 5 seconds to toggle WiFi on or off.  By default, WiFi is turned off.

When WiFi is turned on, Minuet confirms with four quick tones followed by a long high tone.

When WiFi is turned off (default), Minuet confirms with four quick tones followed by a long low tone.

Refer to [these instructions for configuring the WiFi network](#wifi-network).

### Power on restore

Hold `on/off` and `up` together for 5 seconds to toggle power on restore behavior.  By default, power on restore is disabled.

When power on restore is enabled, Minuet will restore the fan operating state, speed, direction, and lid open/close state when it is connected to power.  It confirms this setting with a quick turn followed by a long high tone.

When power on restore is disabled (default), Minuet will leave the fan off and close the lid when it is connected to power.  It confirms this setting with a quick turn followed by a long low tone.

### Keypad indicators

Hold `auto` and `open/close` (`up` and `down` together) for 5 seconds to toggle the behavior of the keypad indicators.  By default, the indicators stay lit or blinking as long as the underlying condition they are indicating remains active.  You can suppress the indicators if you find them distracting.

| Indicator | State | Condition |
| --- | ----- | --- |
| `auto` | solid green | the thermostat is enabled |
| `auto` | blinking green | the thermostat has been manually overridden |
| `rain` | solid red | the rain sensor is disabled (only for models with rain sensors) |
| `rain` | blinking red | the rain sensor detected rain and stopped the fan (only for models with rain sensors)

When keypad indicators are suppressed, they will illuminate for just a few seconds when their condition becomes active and will illuminate again after pressing any key on the keypad while their condition remains active.  Minuet confirms by slow blinking all indicators twice.

When keypad indicators are not suppressed (default), they will illuminate indefinitely while their condition is active.  Minuet confirms by slow blinking all indicators three times.

### Factory reset

Hold `on/off` for 15 seconds to turn the fan off and perform a factory reset.  Minuet confirms with four descending tones then erases all of its settings including saved WiFi credentials.  Follow the [Getting started](#getting-started) guide to get started again.

### Fan motor health monitoring

Minuet monitors the state of the fan motor and automatically stops the fan when it detects a problem.  These problems should be rare and they can often be resolved by waiting for the device to cool, starting the fan again, or by performing maintenance.

Minuet indicates a fan motor fault with three quick tones and it writes the cause to the internal logs.

| Possible cause | Resolution |
| --- | --- |
| Fan motor disconnected | Ensure that the fan motor is plugged in and that its wires are intact. |
| Fan motor stalled | Ensure that the fan blade spins freely and is not obstructed. |
| Overcurrent | Ensure that the fan motor wires are intact. |
| Overtemperature | Allow the device to cool.  Resume operation at a lower speed. |
| Undervoltage or overvoltage | Ensure that the power supply can provide at least 5 amps at 9 to 16 volts. |

If the issue persists, please ask for support.

### Failsafe restart

Minuet monitors the state of its software components and automatically restarts when it detects a problem.  These problems should be rare and they are often resolved automatically by the failsafe restart.

Minuet indicates that a failsafe restart has been triggered with four quick tones and one long tone.  Then, it waits 3 minutes to allow you some time to collect information to help debug the issue.  Finally, it plays the same tones again and restarts the device.

If you have customized the Minuet firmware, please examine the internal logs and review your changes.

If the issue persists, please ask for support.

## Using the 4 key wall remote

The 4 key wall remote has some limitations compares to the built-in keypad and 6 key wall remote.

Because it is designed for a 4 speed fan whereas Minuet supports 10 speeds, the rmeote cycles through 10%, 30%, 70%, and 100%.

When you press any button on the remote while the automatic thermostat is enabled, the remote disables (when using [standard controls](#standard-controls)) or overrides (when using [enhanced controls](#enhanced-controls)) the thermostat before performing the requested action.

### Buttons

- Press `fan on`: turn fan on at its last configured manual fan speed if it was off, otherwise cycle through 4 increasing speeds then back to the lowest speed
- Hold `fan on` for 1 second: turn fan on at maximum speed *(bonus)*
- Press `fan off`: turn fan off
- Press `open`: open lid
- Press `close`: close lid

## Using the Maxxfan infrared remote

Please refer to the instructions originally provided with the remote.

Minuet sets the fan state to match everything that you see on the screen in the remote.  The remote has its own memory of the fan's settings and it may not be completely in sync with the fan.  Sometimes when you press a button to do one thing (such as to change the fan speed) you may observe other settings change too (such as the fan lid closing) because that's what the remote thinks the state should be.

Consequently, there is no difference in the remote's behavior regardless of your choice of [standard](#standard-controls) and [enhanced](#enhanced-controls) controls.

What you see on the infrared remote is what you get.

# Light accessory functions

These additional functions become available when you have installed a light accessory.

## Using the built-in keypad

Use the built-in keypad to control the light as follows.

- Hold `in/out` for 1 second: toggle the light on or off, the light's default color is white
- Hold `in/out` and press `up`: increase the brightness by one step, does nothing if the light is off or is already at maximum brightness
- Hold `in/out` and press `down`: decrease the brightness by one step, does nothing if the light is off or is already at minimum brightness

## Using the 24-key RGBW LED infrared remote control

Use a 24-key RGBW LED remote control to dim the light, change its color, or activate effects as follows.

- Press `on`: turn the light on white, the light's default color is white
- Press `off`: turn the light off
- Press `brightness up`: increase the brightness by one step, does nothing if the light is off or is already at maximum brightness
- Press `brightness down`: decrease the brightness by one step, does nothing if the light is off or is already at minimum brightness
- Press `R`, `G`, `B`, `W`, or any colored button: set the light to the indicated color (approximately), does nothing if the light is off or if it doesn't support changing the color
- Press `Flash`: activate a twinkling color effect, does nothing if the light is off or does not support effects
- Press `Strobe`: activate a pulsing color effect, does nothing if the light is off or does not support effects
- Press `Fade`: activate a solid rainbow color effect, does nothing if the light is off or does not support effects
- Press `Smooth`: activate a chasing rainbow color effect, does nothing if the light is off or does not support effects

Your light accessory kit should include one of these remotes. If you'd like to buy another one, search for "24-key RGBW LED IR remote control" in an online marketplace and you should find some, such as [this listing](https://www.amazon.com/dp/B09C1BFX48). These remotes are fairly generic and inexpensive so they are often included with light fixtures.

You can customize the table of colors and effects by modifying the firmware according to your preferences. Refer to [minuet/accessory/light](https://github.com/brown-studios/minuet-firmware/tree/main/minuet/accessory/light).

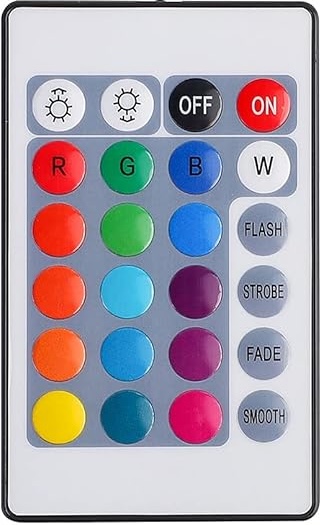
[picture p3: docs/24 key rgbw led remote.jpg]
24-key RGBW LED remote


# WiFi network

There are a few ways to configure the WiFi network.  Choose the appropriate method for your situation.

> [!IMPORTANT]
> Minuet only communicates over the local network to integrate with home automation systems.  Never connect Minuet to public networks!

> [!TIP]
> We recommend configuring your router to assign Minuet a static DHCP entry so that it always receives the same host name and IP address and you can more easily identify it on the network.

## Connect to an existing network with the captive portal (out-of-the-box method)

Use this method to connect to a WiFi network if you just installed Minuet out-of-the-box and haven't modified the firmware.

1. [Turn WiFi on using the keypad](#wifi-mode).  Listen for the tones to confirm that WiFi is on.

1. Connect your smartphone or computer to the `minuet-setup` access point.  Use the password `IAmAFan!`.  If the `minuet-setup` access point does not appear, then perform a [factory reset](#factory-reset) to erase the previous network credentials, and try again.

1. Navigate to [http://192.168.4.1/](http://192.168.4.1/) in your web browser.  It should show the Minuet captive portal.

1. The Minuet captive portal will scan for existing WiFi networks and show them in a list.  Pick your WiFi network from the list or type its SSID into the form.  Type the password for your network into the form.  Click `Save`.

1. Minuet will reboot and attempt to connect to your network.

To connect Minuet to a different WiFi network or to change the network credentials using this method, perform a [factory reset](#factory-reset) to erase the previous network credentials, then start over.

## Configure the network in the firmware (advanced method)

Use this method to compile your WiFi network settings directly into the [Minuet firmware](https://github.com/brown-studios/minuet-firmware) so they are always present and cannot be erased by a factory reset.  It gives you full control over the networking behavior.

We recommend using this method whenever you are customizing the firmware and installing firmware updates over-the-air.

Here are some of the things you can do with this method.

* Connect to one or more existing networks.
* Connect to hidden networks.
* Change or remove the access point credentials, captive portal, and fallback behavior.
* Configure a built-in web server for debugging and remote control.
* Change the API and OTA encryption keys.
* Disable all network features.

Refer to the instructions in [minuet.yaml](https://github.com/brown-studios/minuet-firmware/blob/main/minuet.yaml) and [secrets.yaml](https://github.com/brown-studios/minuet-firmware/blob/main/secrets.yaml) for details.

# Automation

Minuet is designed to support a variety of home automation scenarios.  With a bit of technical effort, you can make Minuet do more for your comfort, automatically.

## Project ideas

Here are some ideas for home automation projects that you could implement.

- Add fan controls to a dashboard elsewhere in your vehicle.
- Schedule the fan to run for a few minutes every day to keep the air fresh.
- Set the thermostat setpoint temperature based on whether your vehicle is occupied.
- When your vehicle engine is running, engage the automation safety lock to turn off the fan to reduce road noise and fumes.
- Synchonize two Minuet fans together so one runs in exhaust while the other runs as an intake at the same speed.
- Coordinate a Minuet fan with other HVAC appliances in your vehicle.

Be creative! ❤️

## How to integrate Minuet with Home Assistant

Home Assistant is an open source home automation platform and it works great for operating a smart house on wheels.

When you integrate Minuet with Home Assistant, you can add the Minuet fan, cover (lid), thermostat, light, sensors, and other entities to you Home Assistant dashboard.  You can also create Home Assistant automations to control Minuet in response to triggers.

1. Connect Minuet to a [WiFi network](#wifi-network) that your Home Assistant server can reach.

1. Wait for Home Assistant to automatically discover Minuet.  If it does not, then follow [these instructions](https://esphome.io/guides/getting_started_hassio/#connecting-your-device-to-home-assistant) to add the ESPHome integration manually.

1. When prompted, enter the API encryption key for your device.  If you have not modified the Minuet firmware, you'll find the encryption key in [secrets.yaml](https://github.com/brown-studios/minuet-firmware/blob/main/secrets.yaml).

1. The Minuet entities will be added to your Home Assistant registry.  Take a look at them and add the ones you want into your dashboard.  Some diagnostic and configuration entities are disabled by default; feel free to enable them if you're curious.

> [!TIP]
> We recommend installing the [ESPHome Builder Add-on](https://esphome.io/guides/getting_started_hassio/) for Home Assistant if you plan to customize the Minuet firmware so that you can control everything in one place.

### Home Assistant dashboard cards

Here is a collection of cards that you can add to your Home Assistant dashboard to control Minuet and customize as you like.

- Fan: Set the fan speed and direction.
- Lid: Open and close the lid.
- Thermostat: Select the active preset, fan mode, lid mode, and manual override behavior.
- Preset: Customize the thermostat presets.

This example requires [custom card features](https://github.com/Nerwyn/custom-card-features).

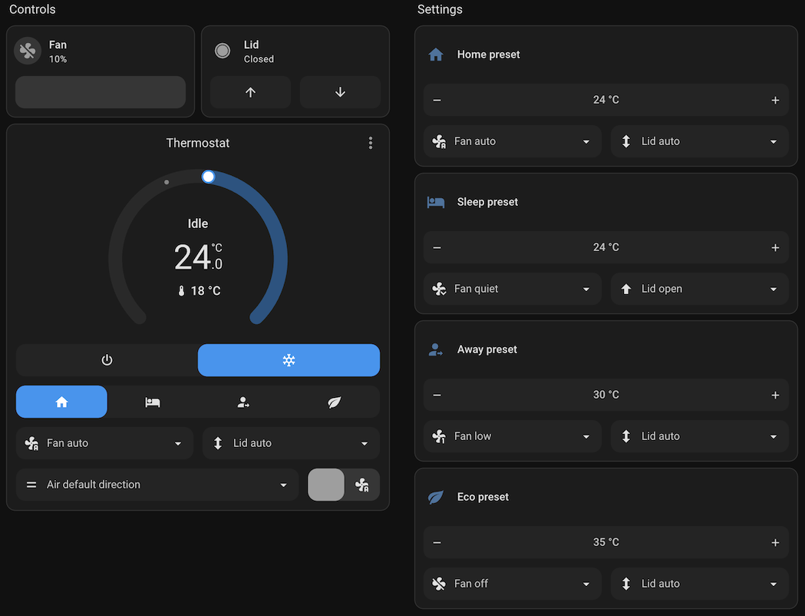
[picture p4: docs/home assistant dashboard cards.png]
Home assistant dashboard cards


<details>
<summary>Example dashboard YAML</summary>

```yaml
type: sections
max_columns: 4
title: Minuet
path: minuet
sections:
  - type: grid
    cards:
      - type: heading
        heading_style: title
        heading: Controls
      - features:
          - type: fan-speed
        type: tile
        features_position: bottom
        vertical: false
        entity: fan.minuet_fan
        name: Fan
        hide_state: false
      - features:
          - type: cover-open-close
        type: tile
        features_position: bottom
        vertical: false
        entity: cover.minuet_lid
        name: Lid
      - type: thermostat
        entity: climate.minuet_thermostat
        features:
          - type: climate-hvac-modes
            style: icons
          - type: climate-preset-modes
            style: icons
            preset_modes:
              - home
              - sleep
              - away
              - eco
          - type: custom:service-call
            entries:
              - type: dropdown
                entity_id: climate.minuet_thermostat
                value_attribute: fan_mode
                options:
                  - entity_id: climate.minuet_thermostat
                    value_attribute: fan_mode
                    option: auto
                    tap_action:
                      action: perform-action
                      perform_action: climate.set_fan_mode
                      target:
                        entity_id:
                          - climate.minuet_thermostat
                      data:
                        fan_mode: auto
                    label: Fan auto
                    icon: mdi:fan-auto
                  - entity_id: climate.minuet_thermostat
                    value_attribute: fan_mode
                    option: quiet
                    tap_action:
                      action: perform-action
                      perform_action: climate.set_fan_mode
                      target:
                        entity_id:
                          - climate.minuet_thermostat
                      data:
                        fan_mode: quiet
                    label: Fan quiet
                    icon: mdi:fan-chevron-down
                  - entity_id: climate.minuet_thermostat
                    value_attribute: fan_mode
                    option: low
                    tap_action:
                      action: perform-action
                      perform_action: climate.set_fan_mode
                      target:
                        entity_id:
                          - climate.minuet_thermostat
                      data:
                        fan_mode: low
                    label: Fan low
                    icon: mdi:fan-speed-1
                  - entity_id: climate.minuet_thermostat
                    value_attribute: fan_mode
                    option: "off"
                    tap_action:
                      action: perform-action
                      perform_action: climate.set_fan_mode
                      target:
                        entity_id:
                          - climate.minuet_thermostat
                      data:
                        fan_mode: "off"
                    label: Fan off
                    icon: mdi:fan-off
              - type: dropdown
                entity_id: select.minuet_thermostat_lid_mode
                options:
                  - entity_id: select.minuet_thermostat_lid_mode
                    option: Auto
                    tap_action:
                      action: perform-action
                      perform_action: select.select_option
                      data:
                        option: Auto
                      target:
                        entity_id: select.minuet_thermostat_lid_mode
                    icon: mdi:arrow-up-down-bold
                    label: Lid auto
                  - entity_id: select.minuet_thermostat_lid_mode
                    option: Open
                    tap_action:
                      action: perform-action
                      perform_action: select.select_option
                      data:
                        option: Open
                      target:
                        entity_id: select.minuet_thermostat_lid_mode
                    label: Lid open
                    icon: mdi:arrow-up-bold
                  - entity_id: select.minuet_thermostat_lid_mode
                    option: Closed
                    tap_action:
                      action: perform-action
                      perform_action: select.select_option
                      data:
                        option: Closed
                      target:
                        entity_id: select.minuet_thermostat_lid_mode
                    label: Lid closed
                    icon: mdi:arrow-down-bold
          - type: custom:service-call
            entries:
              - type: dropdown
                entity_id: select.minuet_thermostat_fan_direction
                options:
                  - entity_id: select.minuet_thermostat_fan_direction
                    option: Default
                    tap_action:
                      action: perform-action
                      perform_action: select.select_option
                      data:
                        option: Default
                      target:
                        entity_id: select.minuet_thermostat_fan_direction
                    label: Air default direction
                    icon: mdi:equal
                  - entity_id: select.minuet_thermostat_fan_direction
                    option: Out
                    tap_action:
                      action: perform-action
                      perform_action: select.select_option
                      data:
                        option: Out
                      target:
                        entity_id: select.minuet_thermostat_fan_direction
                    label: Air out
                    icon: mdi:arrow-up-right-bold
                  - entity_id: select.minuet_thermostat_fan_direction
                    option: In
                    tap_action:
                      action: perform-action
                      perform_action: select.select_option
                      data:
                        option: In
                      target:
                        entity_id: select.minuet_thermostat_fan_direction
                    icon: mdi:arrow-down-right-bold
                    label: Air in
              - type: toggle
                entity_id: switch.minuet_thermostat_manual_override
                tap_action:
                  action: toggle
                  target:
                    entity_id: switch.minuet_thermostat_manual_override
                  data: {}
                unchecked_icon: mdi:fan-auto
                checked_icon: mdi:fan-alert
                styles: |-
                  :host {
                    flex-basis: 120px;
                    --feature-color: var(--red-color);
                  }
        name: Thermostat
  - type: grid
    cards:
      - type: heading
        heading_style: title
        heading: Settings
      - features:
          - style: buttons
            type: numeric-input
          - type: custom:service-call
            entries:
              - type: dropdown
                entity_id: select.minuet_thermostat_preset_home_fan_mode
                options:
                  - entity_id: select.minuet_thermostat_preset_home_fan_mode
                    option: Auto
                    tap_action:
                      action: perform-action
                      perform_action: select.select_option
                      data:
                        option: Auto
                      target:
                        entity_id: select.minuet_thermostat_preset_home_fan_mode
                    label: Fan auto
                    icon: mdi:fan-auto
                  - entity_id: select.minuet_thermostat_preset_home_fan_mode
                    option: Quiet
                    tap_action:
                      action: perform-action
                      perform_action: select.select_option
                      data:
                        option: Quiet
                      target:
                        entity_id: select.minuet_thermostat_preset_home_fan_mode
                    label: Fan quiet
                    icon: mdi:fan-chevron-down
                  - entity_id: select.minuet_thermostat_preset_home_fan_mode
                    option: Low
                    tap_action:
                      action: perform-action
                      perform_action: select.select_option
                      data:
                        option: Low
                      target:
                        entity_id: select.minuet_thermostat_preset_home_fan_mode
                    label: Fan low
                    icon: mdi:fan-speed-1
                  - entity_id: select.minuet_thermostat_preset_home_fan_mode
                    option: "Off"
                    tap_action:
                      action: perform-action
                      perform_action: select.select_option
                      data:
                        option: "Off"
                      target:
                        entity_id: select.minuet_thermostat_preset_home_fan_mode
                    label: Fan off
                    icon: mdi:fan-off
              - type: dropdown
                entity_id: select.minuet_thermostat_preset_home_lid_mode
                options:
                  - entity_id: select.minuet_thermostat_preset_home_lid_mode
                    option: Auto
                    tap_action:
                      action: perform-action
                      perform_action: select.select_option
                      data:
                        option: Auto
                      target:
                        entity_id: select.minuet_thermostat_preset_home_lid_mode
                    icon: mdi:arrow-up-down-bold
                    label: Lid auto
                  - entity_id: select.minuet_thermostat_preset_home_lid_mode
                    option: Open
                    tap_action:
                      action: perform-action
                      perform_action: select.select_option
                      data:
                        option: Open
                      target:
                        entity_id: select.minuet_thermostat_preset_home_lid_mode
                    label: Lid open
                    icon: mdi:arrow-up-bold
                  - entity_id: select.minuet_thermostat_preset_home_lid_mode
                    option: Closed
                    tap_action:
                      action: perform-action
                      perform_action: select.select_option
                      data:
                        option: Closed
                      target:
                        entity_id: select.minuet_thermostat_preset_home_lid_mode
                    label: Lid closed
                    icon: mdi:arrow-down-bold
        type: tile
        features_position: bottom
        vertical: false
        entity: number.minuet_thermostat_preset_home_temperature
        name: Home preset
        hide_state: true
        icon: mdi:home
        grid_options:
          columns: full
      - features:
          - style: buttons
            type: numeric-input
          - type: custom:service-call
            entries:
              - type: dropdown
                entity_id: select.minuet_thermostat_preset_sleep_fan_mode
                options:
                  - entity_id: select.minuet_thermostat_preset_sleep_fan_mode
                    option: Auto
                    tap_action:
                      action: perform-action
                      perform_action: select.select_option
                      data:
                        option: Auto
                      target:
                        entity_id: select.minuet_thermostat_preset_sleep_fan_mode
                    label: Fan auto
                    icon: mdi:fan-auto
                  - entity_id: select.minuet_thermostat_preset_sleep_fan_mode
                    option: Quiet
                    tap_action:
                      action: perform-action
                      perform_action: select.select_option
                      data:
                        option: Quiet
                      target:
                        entity_id: select.minuet_thermostat_preset_sleep_fan_mode
                    label: Fan quiet
                    icon: mdi:fan-chevron-down
                  - entity_id: select.minuet_thermostat_preset_sleep_fan_mode
                    option: Low
                    tap_action:
                      action: perform-action
                      perform_action: select.select_option
                      data:
                        option: Low
                      target:
                        entity_id: select.minuet_thermostat_preset_sleep_fan_mode
                    label: Fan low
                    icon: mdi:fan-speed-1
                  - entity_id: select.minuet_thermostat_preset_sleep_fan_mode
                    option: "Off"
                    tap_action:
                      action: perform-action
                      perform_action: select.select_option
                      data:
                        option: "Off"
                      target:
                        entity_id: select.minuet_thermostat_preset_sleep_fan_mode
                    label: Fan off
                    icon: mdi:fan-off
              - type: dropdown
                entity_id: select.minuet_thermostat_preset_sleep_lid_mode
                options:
                  - entity_id: select.minuet_thermostat_preset_sleep_lid_mode
                    option: Auto
                    tap_action:
                      action: perform-action
                      perform_action: select.select_option
                      data:
                        option: Auto
                      target:
                        entity_id: select.minuet_thermostat_preset_sleep_lid_mode
                    icon: mdi:arrow-up-down-bold
                    label: Lid auto
                  - entity_id: select.minuet_thermostat_preset_sleep_lid_mode
                    option: Open
                    tap_action:
                      action: perform-action
                      perform_action: select.select_option
                      data:
                        option: Open
                      target:
                        entity_id: select.minuet_thermostat_preset_sleep_lid_mode
                    label: Lid open
                    icon: mdi:arrow-up-bold
                  - entity_id: select.minuet_thermostat_preset_sleep_lid_mode
                    option: Closed
                    tap_action:
                      action: perform-action
                      perform_action: select.select_option
                      data:
                        option: Closed
                      target:
                        entity_id: select.minuet_thermostat_preset_sleep_lid_mode
                    label: Lid closed
                    icon: mdi:arrow-down-bold
        type: tile
        features_position: bottom
        vertical: false
        entity: number.minuet_thermostat_preset_sleep_temperature
        name: Sleep preset
        hide_state: true
        icon: mdi:bed
        grid_options:
          columns: full
      - features:
          - style: buttons
            type: numeric-input
          - type: custom:service-call
            entries:
              - type: dropdown
                entity_id: select.minuet_thermostat_preset_away_fan_mode
                options:
                  - entity_id: select.minuet_thermostat_preset_away_fan_mode
                    option: Auto
                    tap_action:
                      action: perform-action
                      perform_action: select.select_option
                      data:
                        option: Auto
                      target:
                        entity_id: select.minuet_thermostat_preset_away_fan_mode
                    label: Fan auto
                    icon: mdi:fan-auto
                  - entity_id: select.minuet_thermostat_preset_away_fan_mode
                    option: Quiet
                    tap_action:
                      action: perform-action
                      perform_action: select.select_option
                      data:
                        option: Quiet
                      target:
                        entity_id: select.minuet_thermostat_preset_away_fan_mode
                    label: Fan quiet
                    icon: mdi:fan-chevron-down
                  - entity_id: select.minuet_thermostat_preset_away_fan_mode
                    option: Low
                    tap_action:
                      action: perform-action
                      perform_action: select.select_option
                      data:
                        option: Low
                      target:
                        entity_id: select.minuet_thermostat_preset_away_fan_mode
                    label: Fan low
                    icon: mdi:fan-speed-1
                  - entity_id: select.minuet_thermostat_preset_away_fan_mode
                    option: "Off"
                    tap_action:
                      action: perform-action
                      perform_action: select.select_option
                      data:
                        option: "Off"
                      target:
                        entity_id: select.minuet_thermostat_preset_away_fan_mode
                    label: Fan off
                    icon: mdi:fan-off
              - type: dropdown
                entity_id: select.minuet_thermostat_preset_away_lid_mode
                options:
                  - entity_id: select.minuet_thermostat_preset_away_lid_mode
                    option: Auto
                    tap_action:
                      action: perform-action
                      perform_action: select.select_option
                      data:
                        option: Auto
                      target:
                        entity_id: select.minuet_thermostat_preset_away_lid_mode
                    icon: mdi:arrow-up-down-bold
                    label: Lid auto
                  - entity_id: select.minuet_thermostat_preset_away_lid_mode
                    option: Open
                    tap_action:
                      action: perform-action
                      perform_action: select.select_option
                      data:
                        option: Open
                      target:
                        entity_id: select.minuet_thermostat_preset_away_lid_mode
                    label: Lid open
                    icon: mdi:arrow-up-bold
                  - entity_id: select.minuet_thermostat_preset_away_lid_mode
                    option: Closed
                    tap_action:
                      action: perform-action
                      perform_action: select.select_option
                      data:
                        option: Closed
                      target:
                        entity_id: select.minuet_thermostat_preset_away_lid_mode
                    label: Lid closed
                    icon: mdi:arrow-down-bold
        type: tile
        features_position: bottom
        vertical: false
        entity: number.minuet_thermostat_preset_away_temperature
        name: Away preset
        hide_state: true
        icon: mdi:account-arrow-right
        grid_options:
          columns: full
      - features:
          - style: buttons
            type: numeric-input
          - type: custom:service-call
            entries:
              - type: dropdown
                entity_id: select.minuet_thermostat_preset_eco_fan_mode
                options:
                  - entity_id: select.minuet_thermostat_preset_eco_fan_mode
                    option: Auto
                    tap_action:
                      action: perform-action
                      perform_action: select.select_option
                      data:
                        option: Auto
                      target:
                        entity_id: select.minuet_thermostat_preset_eco_fan_mode
                    label: Fan auto
                    icon: mdi:fan-auto
                  - entity_id: select.minuet_thermostat_preset_eco_fan_mode
                    option: Quiet
                    tap_action:
                      action: perform-action
                      perform_action: select.select_option
                      data:
                        option: Quiet
                      target:
                        entity_id: select.minuet_thermostat_preset_eco_fan_mode
                    label: Fan quiet
                    icon: mdi:fan-chevron-down
                  - entity_id: select.minuet_thermostat_preset_eco_fan_mode
                    option: Low
                    tap_action:
                      action: perform-action
                      perform_action: select.select_option
                      data:
                        option: Low
                      target:
                        entity_id: select.minuet_thermostat_preset_eco_fan_mode
                    label: Fan low
                    icon: mdi:fan-speed-1
                  - entity_id: select.minuet_thermostat_preset_eco_fan_mode
                    option: "Off"
                    tap_action:
                      action: perform-action
                      perform_action: select.select_option
                      data:
                        option: "Off"
                      target:
                        entity_id: select.minuet_thermostat_preset_eco_fan_mode
                    label: Fan off
                    icon: mdi:fan-off
              - type: dropdown
                entity_id: select.minuet_thermostat_preset_eco_lid_mode
                options:
                  - entity_id: select.minuet_thermostat_preset_eco_lid_mode
                    option: Auto
                    tap_action:
                      action: perform-action
                      perform_action: select.select_option
                      data:
                        option: Auto
                      target:
                        entity_id: select.minuet_thermostat_preset_eco_lid_mode
                    icon: mdi:arrow-up-down-bold
                    label: Lid auto
                  - entity_id: select.minuet_thermostat_preset_eco_lid_mode
                    option: Open
                    tap_action:
                      action: perform-action
                      perform_action: select.select_option
                      data:
                        option: Open
                      target:
                        entity_id: select.minuet_thermostat_preset_eco_lid_mode
                    label: Lid open
                    icon: mdi:arrow-up-bold
                  - entity_id: select.minuet_thermostat_preset_eco_lid_mode
                    option: Closed
                    tap_action:
                      action: perform-action
                      perform_action: select.select_option
                      data:
                        option: Closed
                      target:
                        entity_id: select.minuet_thermostat_preset_eco_lid_mode
                    label: Lid closed
                    icon: mdi:arrow-down-bold
        type: tile
        features_position: bottom
        vertical: false
        entity: number.minuet_thermostat_preset_eco_temperature
        name: Eco preset
        hide_state: true
        icon: mdi:leaf
        grid_options:
          columns: full
cards: []
```
</details>

## How to remotely control Minuet with the ESPHome API

You can directly use the ESPHome API to remotely control Minuet without using Home Assistant.  To connect, you'll need the host name and API encryption key for your device.  If you have not modified the Minuet firmware, you'll find the encryption key in [secrets.yaml](https://github.com/brown-studios/minuet-firmware/blob/main/secrets.yaml).

Start here: [ESPHome API client library](https://github.com/esphome/aioesphomeapi)

## How to customize the Minuet firmware

You can program Minuet to do all sorts of useful things by modifying the firmware and making your own accessories.

Start here: [Minuet firmware](https://github.com/brown-studios/minuet-firmware)

# Minuet app (help wanted)

Minuet does not currently have a smartphone app for remote control.  It'd be lovely have one though.

If you'd like to help build an app for Minuet using Bluetooth LE or the local WiFi network, please contact us!

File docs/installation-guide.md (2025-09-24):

# Minuet installation guide

This guide explains how to install Minuet into your Maxxfan.

- [Main parts](#main-parts)
  - [Getting ready](#getting-ready)
  - [Assembling the brushless fan motor](#assembling-the-brushless-fan-motor)
  - [Disassembling the Maxxfan](#disassembling-the-maxxfan)
  - [Installing the brushless fan motor](#installing-the-brushless-fan-motor)
  - [Connecting the lid motor cable to the lid motor](#connecting-the-lid-motor-cable-to-the-lid-motor)
  - [Connecting the power cable to the electrical supply](#connecting-the-power-cable-to-the-electrical-supply)
  - [Removing the original circuit board from the control panel](#removing-the-original-circuit-board-from-the-control-panel)
  - [Installing the Minuet circuit board into the control panel](#installing-the-minuet-circuit-board-into-the-control-panel)
  - [Reassembling the Maxxfan](#reassembling-the-maxxfan)
  - [Finishing up](#finishing-up)
- [Accessories](#accessories)
  - [Light accessory](#light-accessory)
  - [Cover sensor accessory](#cover-sensor-accessory)

# Main parts

## Getting ready

You're about to upgrade your fan!  It'll be awesome!

Set aside a couple of hours to partially disassemble your fan, install Minuet and your accessories, and reassemble your fan.  Take your time and you'll find the process fairly straightforward.

### Safety check

Confirm that your Maxxfan's electrical supply meets these requirements:

- Voltage: 12 V DC nominal and absolute maximum range from 9 to 16 V DC
- Wiring: minimum 18 AWG (0.8 mm²)
- Circuit protection: 5 A fuse or circuit breaker

This should already be the case if your Maxxfan was installed correctly and it's just good to confirm.

### Supplies

Gather the supplies you will need.

- Parts
  - Minuet fan controller circuit board (already programmed with the Minuet firmware)
  - Fan motor and adapters
  - Wire passage cover
  - Power cable
  - Lid motor cable
  - Zip ties
- Tools
  - #2 Philips screwdriver, short length ("stubby"), to remove fasteners in a confined space under the lid
  - #2 Philips screwdriver, standard length
  - 7/64" allen key
  - 8 mm hex socket driver
  - Additional tools may be needed to assemble the brushless fan motor, if not preassembled

Review the instructions for any [accessories](#accessories) you may have for additional supplies.

## Assembling the brushless fan motor

Retrieve the fan motor, shaft adapter, and mount from your kit.  Assemble them, if not preassembled.

Shaft adapter:

1. Loosely install the grub screws into the 8 mm shaft coupler.
1. Seat the 8 mm dowel pin up to the midpoint of the coupler.  Gently tighten the coupler's grub screws onto the dowel pin.
1. Insert the coupler onto the motor shaft.  Gently tighten the coupler's grub screws onto the dowel pin.

Mount:

1. Screw the M5 screws through the mount from the side on which the motor is installed.  Tighten only until snug to avoid stripping the plastic threads.  Do not use threadlocker.
1. Screw the motor to the plate.  Add a washer on each screw between the screw head and the plate.

## Disassembling the Maxxfan

Start by clearing some space below the fan to work.  You do not need to remove the fan from the roof of your vehicle because all of the necessary fasteners are accessible from inside.

Choose a place to set things down.  Keep the removed parts and fasteners organized while you work to make reassembly easier.

1. Disconnect the electrical supply from the fan (such as by removing its fuse and setting it aside).  For safety, confirm that the fan is non-operational by attempting to turn the fan on (it should remain off).
1. Remove the insect screen by turning the plastic posts that retain it to the fan body until they unlatch.
1. Remove the fan blade from the motor shaft using a 7/64" allen key to loosen the grub screw until the fan blade slides off the shaft.
1. Fully open the lid by turning the lid knob counter-clockwise.
1. Reach up and trace the fan motor wires from the back of the fan motor down to where they are secured to the housing with zip ties.  Cut the zip ties.
1. Continue feeling along the fan motor wires to where they pass under a narrow plastic wire passage cover.  The cover obstructs the wire passage through which the wires enter the fan housing.
1. Feel around the wire passage cover to locate two screw heads on opposite sides.  Removing the cover is awkward because of the limited clearance for tools under the lid (even when fully opened).  Use a short length ("stubby") #2 Philips screwdriver to remove both screws from the cover.  Remove the cover.
1. Remove the lid knob using a #2 Philips screwdriver.
1. Remove the 4 screws that hold the control panel in place using a #2 Philips screwdriver.  These screws were previously hidden under the insect screen.
1. Assess whether you have enough clearance to access the wiring within the fan housing.  If your electrical supply wires or wall control cables are very tight then you may need to remove the trim rim to provide some slack.  Proceed with the next step once you're able to move the control panel a handspan away from the body of the fan.
1. Disconnect the wall controls from the circuit board, if present.
1. Disconnect the rain sensor from the circuit board, if present.
1. Disconnect the lid motor by gently pulling the plug and socket connectors apart.
1. Disconnect the fan motor by gently pulling the plug and socket connectors apart.
1. Disconnect (or cut) the electrical supply.  If you choose to cut these wires, make sure to leave enough slack on both ends to reconnect them later should you have need.
1. Now the control panel should be completely free of the body, set it aside.
1. Use a 8 mm socket driver to remove the M5 nuts that hold the fan motor to the housing and pay attention to the washers under the nuts so you don't lose them!
1. Remove the fan motor and put it away, you won't be needing it anymore but keep the washers and nuts.

That's it with disassembly.

## Installing the brushless fan motor

Assemble the fan motor, shaft adapter, and mount before proceeding.

1. Raise the fan motor into position in the center of the fan housing.  Align the mount's two protruding M5 screws with the mount holes in the housing and seat the mount into place.
1. Secure the mount with the original washers and M5 nuts using an 8 mm socket driver.  Do not overtighten.
1. Drape the fan motor wires along the upper side of the plastic spoke that supports the motor and guide them towards the corner of the housing above the electronics.
1. Pass the fan motor connector through the wire passage.
1. Use two zip ties to secure the fan motor wires to the spoke.

If you are installing a light accessory, proceed to those instructions and install the LED light strip into the housing now.  The light's wires will pass through the same wire passage as the fan motor wires.

Now that all of the wires have been installed through the wire passage in the housing, it's time to reinstall the wire passage cover to protect the electronics from water intrusion.  (Because it is so awkward to remove, you may choose to postpone reinstalling the cover if you anticipate needing to access the wires again soon.)

To reinstall the wire passage cover:

1. The wire passage cover has a notch that fits over the wires where they pass through it.  The notch in the original cover was only big enough for the original 2 motor wires.
    - If your kit includes a new wire passage cover with a bigger notch, use it instead of the original cover.  Or consult the [hardware guide](hardware-guide.md) for instructions on how to make one.
    - Otherwise, you can expand your original wire passage cover to fit over the additional wires.  Carefully carve away excess plastic around the notch until it fits over all of the wires without crimping them.
1. Fully open the lid by turning the lid knob counter-clockwise.
1. Preinstall the screws into the wire passage cover then seat it into place over the wire harness.
1. Tighten down the screws a little bit at a time while checking to ensure that the wires pass through the notch and don't get crimped by the plastic.

Now you can close the lid by turning the lid knob clockwise.

## Connecting the lid motor cable to the lid motor

Attach the Minuet lid motor cable to the lid motor by pressing the plug and socket connectors together.

## Connecting the power cable to the electrical supply

Attach the Minuet power cable to your electrical supply.  Use a vibration-resistant splicing method such as a lever or crimp connector.

Please pay careful attention to the polarity!

- Original Maxxfan power cable: positive is *black*, negative is *white*.
- Minuet power cable: positive is *red*, negative is *black*.  These colors are more conventional.

Make sure you know which is which if you intend to reuse the original wires.  When in doubt, check your electrical supply with a multi-meter before making new connections and label them accordingly.

## Removing the original circuit board from the control panel

Remove the original circuit board from the control panel.

1. Place the control panel onto a flat surface on its back.
1. Unplug the thermistor from the original circuit board.
1. Remove the 3 screws and plastic washers that hold the original circuit board to the control panel.
1. Gently unplug the flexible cable for the built-in keypad from the original circuit board.
1. Now the original circuit board should be free of the control panel, put it away since you won't be needing it anymore.
1. Keep the original screws and plastic washers.

## Installing the Minuet circuit board into the control panel

Ensure that you have completed the set-up process for your minuet circuit board before installing it.

1. Orient the Minuet circuit board with the header labeled **PANEL** facing down into the control panel.  Make sure that the 3 mounting holes line up with the plastic standoffs on the control panel.
1. Gently plug the flexible cable for the built-in keypad to the header labeled **PANEL**.
1. Screw the circuit board into place with the 3 screws and plastic washers that were used for the original circuit board.
1. Plug the thermistor connector into the socket labeled **TEMP**.  You can identify the thermistor by looking for a little black blob that's held into the fan housing with hot glue.  It's a temperature sensor for the thermostat.
1. If you have an accessory that plugs into the **EXPANSION** port, consult its installation instructions then plug it into the socket.  Take care to orient the accessory circuit board to fit within the outline of the main circuit board and ensure that its pins are fully seated.
1. If you have an accessory with a QWIIC interface, plug it into the **QWIIC** connector using a QWIIC cable.

## Reassembling the Maxxfan

During reassembly, it may help to have a second pair of hands to support the control panel while screwing it back into place.

1. Hold the control panel near the unit.
1. Plug the lid motor connector into the socket labeled **LID MOTOR**.
1. Plug the fan motor connector into the socket labeled **FAN MOTOR**.
1. Plug the rain sensor connector into the socket labeled **RAIN**, if you have one.
1. Plug the additional connectors for your accessory, if you have one.
1. Plug the Maxxfan wall control cable into the socket labeled **WALL CONTROL**, if you have one.
1. Plug the power connector into the socket labeled **POWER**.

Before completing the reassembly, optionally give the upgrade a quick test.  Consider enlisting a friend to help.

1. Support the control panel so it doesn't dangle and damage anything.
1. Reconnect the electrical supply (reinstall the 5 A fuse).
1. Press the `on/off` button on the built-in keypad to turn the fan on.  The lid should open and the fan motor should start spinning.
1. Press the `on/off` button again to turn the fan off.  The lid should close and the fan motor should stop spinning.
1. Disconnect the electrical supply (remove the 5 A fuse).

Now complete the reassembly.

1. Raise the control panel into place while guiding and gently tucking the wires into the open space within the housing so they don't get pinched and damaged during reinstallation.  Dress the wires carefully while you work.
1. Screw the control panel into place with the 4 original screws using a #2 Philips screwdriver.
1. Screw the lid knob into place using a #2 Philips screwdriver.
1. Press the fan blade onto the shaft and tighten the grub screw with a 7/64" allen key.  Make sure it spins freely.
1. Install the insect screen and turn the posts that retain it until they latch into place.
1. Reconnect the electrical supply (reinstall the 5 A fuse).

## Finishing up

Congratulations, you have finished installing Minuet!

Read the [user guide](./user-guide.md) and set it up just the way you like.

We recommend keeping the original circuit board and fan motor as a backup.

# Accessories

## Light accessory

Please follow these additional instructions for installing the light accessory.

### Additional supplies

- Parts
  - Minuet light accessory circuit board
  - LED light strip
  - 24-key RGBW LED infrared remote control

### Installing the light

After removing the fan blade, the wire passage cover, and the control panel...

- Watch this [video explanation](https://vimeo.com/1115025239/6b51f73794) for how to position the LED strip.
- Thoroughly clean the rim of the fan housing all the way around its circumference.
- Wipe the rim with alcohol to remove any remaining oils and ensure proper adhesion of the LED strip.  Allow to dry.
- Pass the LED strip connector and wire down through the wire passage above the electronics.
- Hold the head of the LED strip (the end with the wires attached) up to the rim of the fan housing in the corner nearest the electronics.  Align it with the underside of the plastic spokes that support the fan motor.  Confirm that you can wrap the LED strip all the way around the rim of the fan housing in a counter-clockwise loop as you look up into the fan.
- Peel back part of the adhesive release liner and press the LED strip where you held it.  Incrementally peel and apply the LED strip in a counter-clockwise loop as you look up into the fan.  Don't peel the whole release liner all at once!
- Press the LED strip firmly into place all the way around to activate the adhesive.

### Connecting the light

After plugging the main connectors into the Minuet circuit board...

- Plug the LED strip connector into the accessory circuit board socket labeled **LIGHT**.

### Testing the light

After connecting the electrical supply...

- Press and hold the `in/out` button for a second.  The light should turn on.
- Use the 24-key RGBW LED infrared remote control to change the color.
- Press and hold the `in/out` button for a second.  The light should turn off.

## Cover sensor accessory

Please follow these additional instructions for installing the cover sensor accessory.

### Additional supplies

- Parts
  - Cover sensor
  - Insulated vent cover (not included)
  - Magnet (optional, not included)
  - Gaffer's tape (not included)
- Tools
  - Multimeter (optional)

### Installing the cover sensor

After removing the control panel...

- Unscrew and remove the trim ring from the ceiling.
- Determine where to install the cover sensor:
  - If your insulated vent cover attaches to the trim ring with magnets, choose a non-essential magnet to remove from the trim ring.  Remove the magnet and mark the location for the cover sensor on the back side of the trim ring.
  - If your insulated vent cover doesn't have magnets, attach (sew, tape, or glue) a magnet to your vent cover somewhere along its perimeter where it comes into contact with the trim ring.  Mark the corresponding location for the cover sensor on the back side of the trim ring.
- Use gaffer's tape (or similar) to secure the cover sensor to the back side of the trim ring at the location that you marked.

Optional: To confirm the location of the cover sensor before you complete the installation, use a multimeter to test continuity between the two pins of the connector.  The circuit should be closed when you attach your insulated vent cover to the trim ring; otherwise the circuit should be open.

- Consider how to route the cover sensor cable from the sensor to the electronics in the corner of the fan housing.  The cover sensor cable will need to run along the back side of the trim ring towards the corner then invisibly tuck over or pass through a notch in the shroud to reach the electronics.
- Use more gaffer's tape (or similar) to secure the cover sensor cable along the route that you selected.
- Carefully reinstall the trim ring to the ceiling such that the cover sensor connector enters the fan housing near the electronics.

### Connecting the cover sensor

After plugging the main connectors into the Minuet circuit board...

- Plug the cover sensor connector into the socket labeled **LOCK**.

### Testing the cover sensor

After finishing the installation...

- If the fan is off, press the `on/off` button.  The fan should turn on.
- Attach the insulated vent cover.  The fan should turn off.
- Remove the insulated vent cover.  The fan should remain off (unless the thermostat turns it on automatically).

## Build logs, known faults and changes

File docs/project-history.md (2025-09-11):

# Minuet project history

Minuet has come a long way!

I started Minuet as a little rainy day project to save me from the madness of my squeaking Maxxfan motor and to learn about making consumer electronics.  The project has been successful on both counts!  And it's grown beyond my original goals to become a consumer product and not just a simple one-off build.

Here's a taste of how Minuet has evolved over time.

You might also be interested in the [Minuet build log](https://vimeo.com/showcase/11858950).

## November 2024: Early motivation

That month, it rained a lot and I had to pause my campervan build.  Eager to find something to do, I turned my attention to my Maxxfan.

I had been sketching out designs for a home automation interface that would plug into the Maxxfan's remote control ports.  It seemed like I could make some hardware to simulate key presses.  Several folks had made devices similar to this already and I wanted to experiment with passively scanning the keypad to monitor when the user pressed keys so that I could keep the home automation system in sync with manual actions on the fan keypad.  It was getting a bit complicated and I wasn't satisfied with the inherent limitations of that approach.

It was the squeaking that did it.  My Maxxfan fan motor made an awful squeaking noise while running.  Two or three times a second, squeak-squeak-squeak.  It drove me mad!  I had cleaned the motor a couple of times but the squeaking never went away for long.

It occurred to me that I could solve both problems at once with an ESP32 microcontroller and a brushless fan motor...

## December 2024: Minuet v1

I wasn't sure this idea was going to work so I tried to keep it simple.

The [Minuet v1 circuit board](https://github.com/brown-studios/minuet/blob/v2.x/hardware/minuet/v1/design-and-errata.md) proved out the basic operation of the BLDC fan motor, lid motor, built-in keypad, and integration with Home Assistant, while omitting non-essential functions like remote controls.

I initially used an off-the-shelf 15 W BLDC motor for the fan.  I made a laser cut aluminum adapter plate with standoffs to mount the motor into the Maxxfan fan housing and I added a shaft coupling and dowel to extend the shaft as required.  I tediously hand-assembled the PCB, programmed the ESPHome firmware, and bodged around hardware bugs.  And it worked great!

Now that I had solved my problem, I started telling people about Minuet on forums.  Lots of folks seemed to want one too and that encouraged me to continue iterating on the design.

Since I wanted to share my designs and I knew they weren't perfect, I recorded my errata alongside the hardware design files in case someone might try to build one themselves.  One thing that didn't work so well was the DRV10970 motor driver chip: it was underpowered and the quieter sinusoidal modulation didn't work properly when driving the motor in reverse.  So I iterated.

## January 2025: Minuet v2.0

Now that I had floated the idea of making kits, I decided to flesh out the Minuet feature set to meet the needs of more people.

The [Minuet v2.0 circuit board](https://github.com/brown-studios/minuet/blob/v2.x/hardware/minuet/v2/design-and-errata.md) achieved feature parity with the original Maxxfan control board. It added support for the an IR remote control, wire wall controls, rain sensor, thermostat, piezo buzzer for (polite and configurable) audible feedback, and had a more powerful BLDC fan motor driver.  The new MCT8315 motor driver chip really was significantly more powerful and I upgraded to a 50 W BLDC motor.  For fun, I included a little easter egg for the audible feedback (can you find it?).

The [Light and load accessory v2 circuit board](https://github.com/brown-studios/minuet/blob/v2.x/hardware/load/design-and-errata.md) added lights to the fan.  It was designed to control two independent or one addressable LED strip with voltage selection jumpers.  Unfortunately, there were hardware issues and it couldn't drive the data line fast enough for the addressable LED strip.  I decided to scrap this design and focus only on lighting for the next version.

Now that Minuet was feature complete, the fan really came to life!  (With some bugs...)

## February 2025: Minuet v2.1

The next version was an incremental improvement.

The [Minuet v2.1 circuit board](https://github.com/j9brown/minuet/blob/v2.x/hardware/light/v2/design-and-errata.md) upgraded the MCT8315 motor driver chip to MCT8316 that could handle twice the current and it fixed a bunch of hardware bugs.

The [Light accessory v2.5 circuit board](https://github.com/j9brown/minuet/blob/v2.x/hardware/light/v2/design-and-errata.md) superseded the earlier light and load accessory to only focus on driving a PWM or addressable LED light.  This much simpler design worked much better and finally I could make rainbow colors dance around my fan.

Minuet v2.1 worked very well except that the motor wasn't operating as quietly as I liked.  It didn't squeak but it make a soft ticking sound due to uneven torque produced by trapezoidal commutation.  I felt that I needed to solve this problem if I was going to claim that Minuet really was a quiet fan upgrade.

## May 2025: Minuet v3.0 (current release)

Minuet v3 is a big step towards making a real product that can be manufactured and continues improving beyond the feature set of the original Maxxfan.  This is the first version of Minuet to be fabricated with JLCPCB's PCBA service (no more tedious hand-soldering).

The [Minuet v3 circuit board](../hardware/minuet/v3/design-and-errata.md) uses a MCF8316D fan motor driver with field-oriented control that makes the fan motor run much quieter than before.  It solves the commutation noise problem and it no longer needs hall effect sensors so a wider range of motors can be used.  The expansion port has been expanded with more GPIO pins for accessories.  The new safety lock feature stops the fan and shuts off the light when engaged.

The [Light accessory v3 circuit board](../hardware/light/v3/design-and-errata.md) is an incremental upgrade to the previous light accessory for the new expansion port and it added a small through-hole prototyping area for customization.

The cover sensor accessory detects that an insulated vent cover has been attached using a normally-open reed switch attached to the safety lock port.  It is very convenient!

Overall, Minuet v3.0 is approaching the quality of a finished product.

## What comes next

Our next tasks are finalizing the design, working with manufacturers to fabricate kits with everything you will need to upgrade your Maxxfan, and planning for order fulfillment.  We are also investigating the possibility of manufacturing custom brushless fan motors that will fit into the fan housing with fewer adapters.

Please contact us if you would like to contribute your manufacturing experience to this project.

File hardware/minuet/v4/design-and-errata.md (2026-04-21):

# Minuet v4.0

**Status: UNDER DEVELOPMENT, UNTESTED**

The Minuet fan controller circuit board upgrades the Maxxfan with a quiet brushless fan motor driver and home automation features.

## Design synopsis

The microcontroller is an [ESP32-C6-MINI-1](https://documentation.espressif.com/esp32-c6-mini-1_mini-1u_datasheet_en.pdf) with 8 MB of flash, 160 MHz CPU, WiFi 802.11ax, Bluetooth 5 LE, Zigbee/Thread, and an integrated 2.4 GHz antenna.  It is ample for running ESPHome and low power.  Documentation: [Technical reference manual](https://documentation.espressif.com/esp32-c6_technical_reference_manual_en.pdf)

The fan motor driver is a [MCF8316D](https://www.ti.com/lit/ds/symlink/mcf8316d.pdf).  It supports sensorless brushless DC motors with field oriented control with current limiting, built-in motor parameter estimation, and I2C interface.  The integrated buck converter is disabled as per this [application note](https://www.ti.com/lit/an/slla643/slla643.pdf).

The lid motor driver is a [DRV8876](https://www.ti.com/lit/ds/symlink/drv8876.pdf).  The current sense pin is connected to an ADC pin to detect lid end-of-travel.

The [TCA9555](https://www.ti.com/lit/ds/symlink/tca9555.pdf) IO expander on-board provies an 16 additional IO pins with built-in pull-up resistors via I2C.

The [TPS561201](https://www.ti.com/lit/ds/symlink/tps561201.pdf) buck converter supplies 1 A at 3.3 V.  It is optimized for high efficiency with pulse skipping for low power operation.

The [TSOP39238](https://www.vishay.com/docs/82778/tsop392.pdf) IR receiver supports the Maxxfan IR remote control.

The `EXPANSION` port enables accessories and factory programming.  It exposes GPIOs, the serial port, the I2C bus, the safely lock signal, the reset and bootloader signals, and the 3.3 V and 12 V power rails.  You can make your own accessories to plug into this port.

The `I2C` port allows readily available QWIIC compatible I2C accessories to be connected with ease.

The `TEMP` port connects to the Maxxfan's built-in thermistor for use by the automatic thermostat.

The `RAIN` port connects to the Maxxfan's rain sensor (only certain models).

The `LOCK` port triggers a safety lock function that stops the fan, closes the lid, and inhibits operation.

The USB-C port and the `BOOT` and `RESET` tactile switches are used for accessing the bootloader and programming the firmware.

A simple voltage divider measures the supply voltage and triggers a software-controlled low battery protection function.

A piezo buzzer provides audible feedback.  Minuet aims to be polite about its use of audible feedback.  It can be configured in software or disabled in hardware by cutting the `SOUND` jumper trace.

[View the schematics in PDF format](minuet.pdf)

## Circuit board

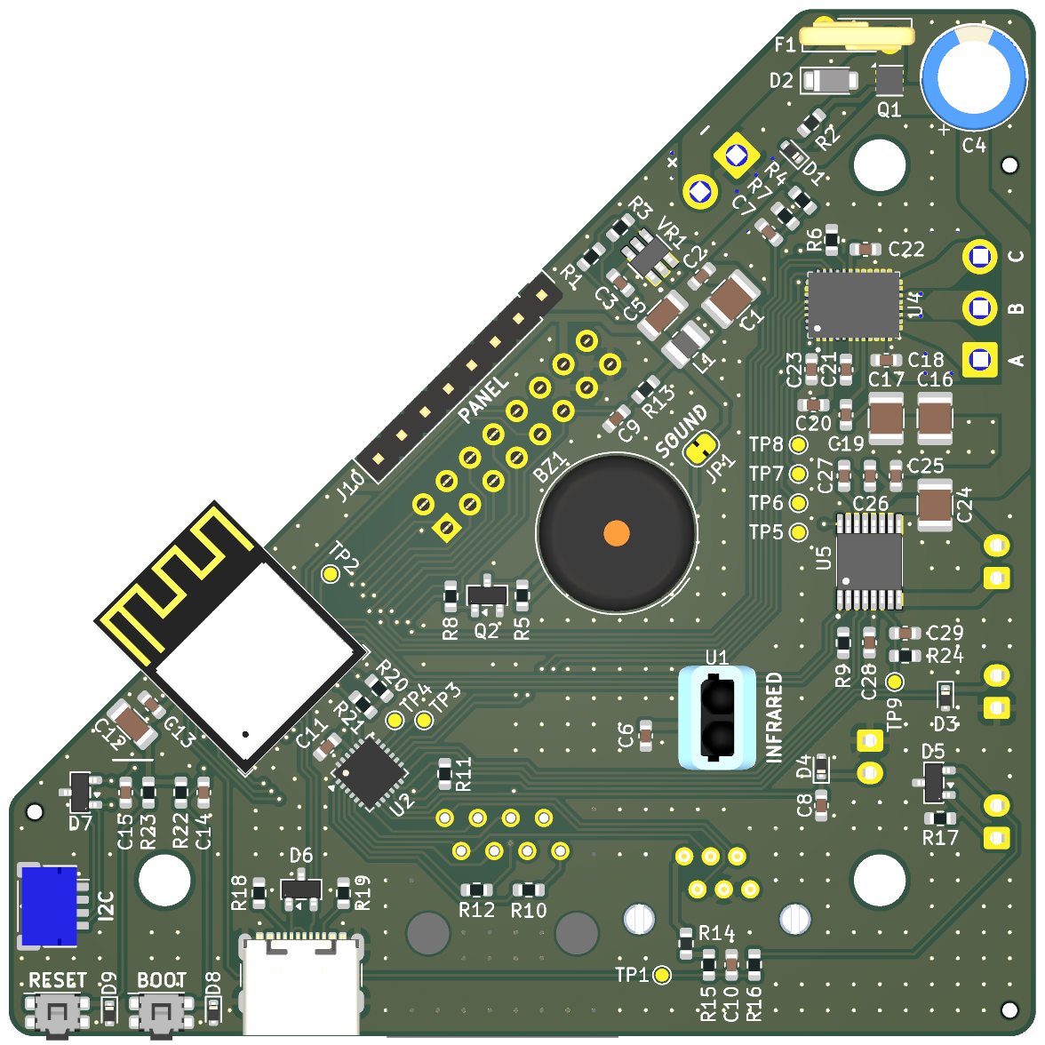
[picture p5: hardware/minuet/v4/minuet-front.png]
Front side of circuit board


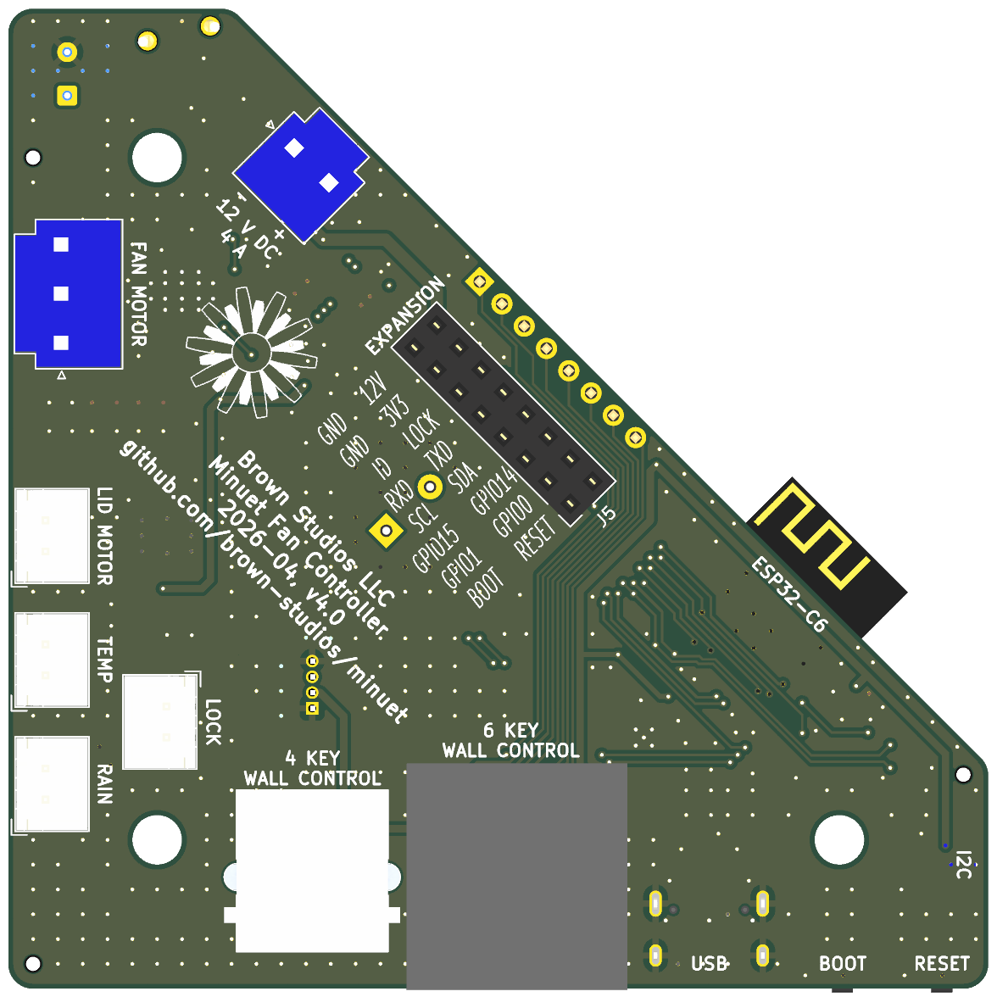
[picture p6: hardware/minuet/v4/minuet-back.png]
Back side of circuit board


## Recommended operational parameters

Recommended electrical supply specifications:

- Voltage: 12 V DC nominal and absolute maximum range from 9 to 16 V DC
- Wiring: minimum 18 AWG (0.8 mm²)
- Circuit protection: 5 A fuse or circuit breaker

Recommended motor specifications:

- Fan motor: Brushless DC motor rated for the supply voltage and continuous duty, no hall sensors needed, driven with up to 4 A current per phase
- Lid motor: Brushed DC motor rated for the supply voltage and intermittent duty, can draw up to 2 A current

Please test your set up carefully and monitor heat dissipation if you choose to operate Minuet beyond these recommendations.

## PCB assembly

The KiCad project contains the bill of materials.  It includes part numbers and orientations of all SMT components for the JLCPCB PCBA service.

You will need advanced soldering skills if you assemble this project by hand.  Several parts have very fine pitch pads that are inaccessible from the sides and require a solder stencil, fine solder paste, and a temperature controlled hot plate or a reflow oven.  The fan motor driver chip in particular must be carefully soldered to ensure an efficient thermal bond to the PCB.

All of the SMT components are on the front side of the board.  They should be soldered first before moving on to the through hole components.

There are through hole components on both sides of the board.  Follow the silkscreen courtyard markings to determine the correct orientation.

The 1x8 pin header labeled `PANEL` must have a sufficient mating contact length to securely attach the keypad's flex connector.  The BOM specifies a part with an 8.1 mm mating contact length that works well.  Shorter contacts may be fine but the connector could come loose under vibration so be sure to check the fit.

The IR receiver must be raised above the board as far as the leads can be extended (about 16 mm) to be visible through the clear window in the keypad.  Thus the IR receiver will need mechanical support to keep it propped up and to insulate the leads.  You can 3D print a suitable standoff from [this model](https://cad.onshape.com/documents/11f07c0bb608e7010778ac35/w/a82f75dceda39e564795dbd4/e/5949b73994c9747af7d1d4c9) or make your own using other materials such as cardboard.

You can safely omit certain components that you don't need including the IR receiver, the 6P6C and 8P8C connectors for wired wall controls, the rain sensor circuitry, and the piezo buzzer.

To improve the circuit board's moisture resistance, you can spray it with an insulative conformal coating after taking care to mask off all connectors before spraying so they don't get coated unintentionally.

## Fabrication

Use the `JLCPCB fabrication toolkit` plug-in to generate files for JLCPCB.

Fabrication parameters:

- Material: 4 layers, FR4 TG155, ENIG, 1 oz outer copper, 0.5 oz inner copper
- Via covering: plugged (to improve moisture resistance)
- Min via hole size: 0.3 mm (default)
- Board outline tolerance: 0.2 mm (default)
- PCBA type: standard or economic
- Assembly side: top and bottom, or just the top if you plan to assemble the bottom connectors manually
- Edge rails: by JLCPCB
- Tooling holes: by customer
- Parts selection: by customer
- Solder paste: high temp (default)
- Conformal coating: both sides
  - Do not spray connectors
  - Do not spray U1 pads (infrared receiver will be assembled later)
  - Do not spray BZ1 sound hole

## Setup

### Temperature sensor

Connect the Maxxfan's temperature sensor to the `TEMP` port.  You can make your own temperature sensor connecting any 10 Kohm NTC thermistor to a JST XH-2 plug in any orientation.  Update the thermistor beta constant in the firmware to ensure accurate readings.

The temperature sensor is driven by an IO pin to minimize resistive self-heating and power usage between samples.  The Maxxfan's built-in thermistor appears to have a beta constant of 3950.

### Rain sensor

Connect the Maxxfan's rain sensor to the `RAIN` port, if your unit has one.

If your unit doesn't have a rain sensor, then you probably don't need one because the lid cover already keeps the water out and it is safe to operate the fan in the rain.  To experiment with the rain sensor function, you can buy an OEM replacement rain sensor or make your own rain sensor by mounting two parallel wires to a surface that's exposed to the rain such that water drops will form a conductive path between them.  Connect the wires to a JST XH-2 plug in any orientation.

The rain sensor circuit uses the ADC to detect a small current flowing between bare electrodes immersed in water.  The circuit has high impedance and ESD protection diodes to protect itself from the environment.

### Safety lock

Connect a switch to the `LOCK` port with a JST XH-2 plug to trigger a safety lock function that that stops the fan, closes the lid, and inhibits operation.  You can connect several switches in parallel to inhibit operation under a multitude of external conditions.

Here are some suggested applications:

- Attach a magnet to your insulated vent cover and a normally-open reed switch connected to the `LOCK` port somewhere in the fan trim ring or ceiling to inhibit operation while the insulated vent cover is installed.
- Connect a relay or optocoupler to inhibit operation of the fan while the engine is running.

Pin 1 is ground.  Pin 2 is a digital input with a pull-up to 3.3 V.  The safety lock engages when pin 2 is low (tied to ground) and disengages when pin 2 is floating.

### Piezo buzzer

The piezo buzzer is designed with politeness in mind which may be a matter of personal preference.

You can customize or disable audible feedback in the device settings or firmware.

You can physically disable the buzzer in hardware by cutting the `SOUND` jumper trace on the board.

And if you want to make the fan play a cheerful jingle then you can change the firmware to do that using [RTTTL](https://en.wikipedia.org/wiki/Ring_Tone_Text_Transfer_Language).

### Fan motor

Connect a suitably rated brushless motor to the `FAN MOTOR` port with a JST VH-3 plug.  Pin 1 is phase A, pin 2 is phase B, pin 3 is phase C.  If the motor operates in the reverse direction than you expect, simply swap any two phases.

Configure the motor parameters in the firmware.

The [MCF8316D](https://www.ti.com/lit/ds/symlink/mcf8316d.pdf)] is configured to mostly be controlled and monitored over I2C instead of spending precious GPIOs on digital logic signals.  The buck converter is disabled because it isn't needed.  Minuet is not compatible with any other revisions of the MCF8316 chip because they have substantially different register layouts.

Note: The MCF8316D has a [known issue](https://e2e.ti.com/support/motor-drivers-group/motor-drivers/f/motor-drivers-forum/1555307/mcf8316d-brake-triggers-watchdog_fault-when-watchdog-is-enabled/5991916) that causes a spurious watchdog timeout when tickling the watchdog over I2C.  Minuet uses the external watchdog pin to tickle the watchdog as a workaround.

### Lid motor

Connect the Maxxfan's lid motor to the `LID MOTOR` port with a JST XH-2 plug.

The lid motor driver automatically limits the motor current using current chopping with a fixed off-time.  If the current exceeds the driver chip's fixed overcurrent threshold (3.5 A to 5 A), the motor driver reports an overcurrent fault and latches the output off to prevent damage.  An overcurrent fault may indicate a physical problem with the motor or other components.

The lid motor draws current proportional to the work it must do to move the lid.  As the lid begins to move, the motor draws more current to overcome friction and inertia in the mechanism, then the current reduces as the lid moves towards its final position, and finally the current increases significantly once the lid reaches its end of travel and the motor stalls.

The Maxxfan does not have a limit switch to sense when the lid has reached end of travel so Minuet monitors the lid motor current and waits for the current to exceed a programmed stall current threshold `I_STALL` for a certain period of time then stops the motor.

The DRV8876 produces a current at the `I_PROPI` pin in proportion to the motor current.  The `R_PROPI` resistor transforms the current into a voltage called `V_PROPI`.  When the voltage at `V_PROPI` reaches `V_REF`, the motor current has exceeded the trip current `I_TRIP` and DRV8876 performs current chopping.  Minuet monitors the motor current by sensing the voltage at `V_PROPI` with an ADC.

Let's determine the appropriate values for `V_REF` and `R_PROPI`.

First we consider the range of the ADC.  According to the datasheet, the ESP32-C6 ADC has an calibrated measurement range of 0 to 3300 mV with +/- 40 mV error when sampled with 12 dB attentuation.  For this application, Minuet only needs to detect when the value exceeds a coarsely defined stall current threshold (perhaps set `I_STALL` to be 80% of `I_TRIP`) and absolute precision near the ends of the range isn't important.  So for convenience, we can set `V_REF` to 3.3 V.

Next we consider the trip current for current limiting, `I_TRIP`.  The Maxxfan lid motor (P/N 10-20270) needs about 300 mA at 12 V to start moving, draws less than 100 mA while coasting to a closed position, may draw as much as 600 mA or more when it encounters significant resistance, and may draw more current to operate with increasing age and wear.  The maximum current rating of the motor is unknown but it does not appear to be damaged when driven with 1.5 A for a few seconds.  For convenience, choose `I_TRIP` to 1 A and set `I_STALL` to 800 mA.

`R_PROPI` = 1000 * `V_REF` / `I_TRIP` = 1000 * 3.3 V / 1 A = 3.3 Kohm

If your lid motor stalls prematurely while opening or closing the lid, try cleaning the motor first.  If that doesn't help, try increasing the `I_STALL` threshold in the firmware.  If all else fails, you can try increasing `I_TRIP` to 1.5 A by reducing `R_PROPI` to 2.21 Kohm.

### Expansion port

Connect Minuet accessories to the `EXPANSION` header.

And you can make your own accessories too!

The `EXPANSION` header includes the following signals.  Refer to the Minuet schematics or the circuit board silkscreen for the complete pinout.

- `GPIO0`, `GPIO1`, `GPIO14`, `GPIO15` can be used for any purpose
- `UART_RXD` and `UART_TXD` provide the serial port
- `I2C_SCL` and `I2C_SDA` provide the I2C bus (QWIIC)
- `RESET` and `BOOT` are wired in parallel with their corresponding buttons (active low)
- `LOCK` engages the safety lock (active low)
- `ACC_ID` [identifies the accessory](#accessory-identification) that is plugged into the expansion port (see below)
- 12 V supply is unregulated, 1 A current available
- 3.3 V supply is regulated, 600 mA current available
- Ground

The accessory PCB should be no larger than 30 mm x 30 mm to ensure it fits within the housing.  It has a 16-pin 2-row pin header with 2.54 mm pitch centered 7.5 mm from the upper edge.

> [!TIP]
> Refer to the [light accessory](../../light) as an example for the connector placement and PCB layout.  And by closing the custom accessory ID solder jumper (labeled `CUSTOM ACC ID` on the board), you can also repurpose the circuit board to build completely custom accessories with the provided signal pin breakout and prototyping area.

### Accessory identification

Minuet needs to identify which accessory is plugged into the expansion port so it can configure the expansion port GPIO pins and ESPHome entities correctly.  On boot, the firmware measures the voltage of the `ACC_ID` pin with an ADC channel and sets things up accordingly.

The `ACC_ID` pin forms the center terminal of a voltage divider.  The Minuet main circuit board has a `100K` resistor from `ACC_ID` to the 3.3 V supply.  The accessory circuit board identifies itself with a resistor `R_ACC_ID` from `ACC_ID` to ground as shown in the following table.  Use resistors with 1% tolerance to ensure accurate identification and allow for future expansion.

| ID | Accessory resistor (`R_ACC_ID`) | Voltage at `ACC_ID` | Usage |
| -- | --- | --- | ----- |
| 0  | none (open circuit) | 3.3 V | no accessory connected |
| 1  | 0 ohm (short circuit) | 0 V | custom accessory |
| 2  | 100 Kohm +/- 1% | 1.65 V | light accessory |
| 3  | 68 Kohm +/- 1% | 1.34 V | reserved |
| 4  | 47 Kohm +/- 1% | 1.06 V | reserved |
| 5  | 33 Kohm +/- 1% | 0.82 V | reserved |
| 6  | 22 Kohm +/- 1% | 0.60 V | reserved |
| 7  | 15 Kohm +/- 1% | 0.43 V | reserved |
| 8  | 10 Kohm +/- 1% | 0.30 V | reserved |
| 9  | 150 Kohm +/- 1% | 1.98 V | reserved |
| 10 | 220 Kohm +/- 1% | 2.27 V | reserved |
| 11 | 330 Kohm +/- 1% | 2.53 V | reserved |
| 12 | 470 Kohm +/- 1% | 2.72 V | reserved |

If you are developing a custom accessory for personal use, please connect `ACC_ID` to ground to prevent the firmware from attempting to configure the accessory itself because your own customized ESPHome YAML configuration will take care of it.  We recommend using a zero ohm resistor so you can assign an ID later.

If you are developing an accessory for broader distribution, please open an issue in the Minuet firmware repository to allocate an ID for your accessory and provide an accessory driver to ensure a convenient plug-and-play experience for end-users.

> [!NOTE]
> We decided to use a resistor for accessory identification to keep it simple for folks who want to design their own expansion port accessories.  We also considered using an I2C EEPROM to store identification and configuration information but it didn't seem necessary.

### I2C port

Connect [QWIIC](https://www.sparkfun.com/qwiic) compatible peripherals to the `I2C` port, such as the Minuet environmental sensor, to this port.

## Details

### IO pins

The ESP32-C6 microcontroller pins are assigned to usages that need special functions.  The expansion port pins have been chosen to have relatively few constraints on their usage to ease accessory development.

| Pin | Usage | Reset state | Function | Remarks |
| --- | ---  | --- | --- | --- |
| GPIO0  | Expansion port | floating | GPIO, ADC, XTAL+, etc. | |
| GPIO1  | Expansion port | floating | GPIO, ADC, XTAL-, etc. | |
| GPIO2  | Rain sensor | floating | ADC | |
| GPIO3  | Thermistor | floating | ADC | |
| GPIO4  | Lid motor current sensor | floating | ADC | JTAG MTMS, strapping pin (irrelevant because SDIO not used) |
| GPIO5  | Voltage sensor | floating | ADC | JTAG MTDI, strapping pin (irrelevant because SDIO not used) |
| GPIO6  | Accessory ID | pull-up | ADC | JTAG MTCK, internal pull-up active on boot unless EFUSE_DIS_PAD_JTAG = 1 |
| GPIO7  | Piezo buzzer | floating | LEDC PWM | JTAG MTDO |
| GPIO8  | I2C data | floating | I2C SDA | external pull-up, strapping pin (high to allow download mode) |
| GPIO9  | BOOT button | floating | GPIO | external pull-up, strapping pin (select boot / download mode) |
| GPIO12 | USB data | floating | USB D- | |
| GPIO13 | USB data | pull-up | USB D+ | |
| GPIO14 | Expansion port | floating | GPIO, etc. | |
| GPIO15 | Expansion port | floating | GPIO, etc. | strapping pin (irrelevant because EFUSE_JTAG_SEL_ENABLE = 0) |
| GPIO16 | Console serial port TX | pull-up | UART0 TX | |
| GPIO17 | Console serial port RX | pull-up | UART0 RX | |
| GPIO18 | I2C clock | pull-up | I2C SCL | external pull-up |
| GPIO19 | IR receiver | pull-up | RMT | receiver has integrated pull-up |
| GPIO20 | Lid motor driver IN2 | pull-up | GPIO | |
| GPIO21 | Lid motor driver IN1 | pull-up | GPIO | |
| GPIO22 | Fan driver watchdog | pull-up | GPIO | |
| GPIO23 | Reserved for future use  | pull-up | GPIO | |

The TCA9555 IO expander handles the remaining low speed digital logic functions.  These pins are designated with the `XIO` prefix in the schematics.  They have always-on internal 100 Kohm pull-ups and are configured as inputs at reset.

| Pin | Usage | Remarks |
| --- | ---  | --- |
| XIO0 | Keypad LED "auto" | active low |
| XIO1 | Keypad LED "rain" | active low |
| XIO2 | Keypad column 3 | |
| XIO3 | Keypad row 2 | |
| XIO4 | Keypad column 4 | |
| XIO5 | Keypad column 2 | |
| XIO6 | Keypad row 1 | |
| XIO7 | Keypad column 1 | |
| XIO8 | Safety lock | active low |
| XIO9 | Thermistor power | active high |
| XIO10  | Lid motor driver fault | active low |
| XIO11  | Lid motor driver sleep | active low |
| XIO12  | Fan motor driver fault | active low |
| XIO13  | Fan motor driver wake | active high |
| XIO14  | Reserved for future use  | |
| XIO15  | Reserved for future use  | |

Pins marked as reserved for future use are provided as test points on the circuit board.

### Capacitor DC bias derating

The ceramic bulk capacitors on the 12 V supply are sized to compensate for the loss of capacitance due to DC bias.  A typical 10 uF MLCC with a 12 V DC bias might be derated by as much as 80% in 0805 size but only by 25% in 1210 size so this design uses physically larger capacitors with an X5R or X7R dielectric for those applications.

### Via stitching pattern

The via stitching pattern is mostly generated with the `kicad-action-scripts` plug-in and additional vias added by hand where needed.  Stitching couples the inner ground planes and outer copper pours to reduce radiated emissions and improves thermal dissipation.

Parameters for the plug-in:

- Via copper size: 0.5 mm
- Via drill size: 0.3 mm
- Via clearance: 0.3 mm
- Via grid: 2.0 mm
- Net name: GND
- Pattern: rectangular

## Errata

Nothing yet...

## Changelog

Changes since v3:

- Replace the ESP32-C3 with an ESP32-C6 to alleviate GPIO scarcity and provide more options for radio connectivity.
- Use a 4 layer PCB with signal/ground/ground/signal stack-up, copper pours, and via stitching to improve thermal dissipation, power distribution, and EMC.
- Increase local bulk capacitance for the motor drivers taking DC bias derating into account.
- Add reverse polarity protection.
- Add ESD protection to external signals.
- Use the ADC to monitor the lid motor current to detect end of travel in software.
- Remove trim potentiometer for the lid motor current limit.
- Provide PWM signals to the lid motor driver to support soft start.
- Use the ADC to detect rain instead of a comparator to reduce the bill of materials.
- Change the footprint of the 6P6C connector to one that is more commonly available.
- Identify the accessory plugged into the expansion port
- Adjust the position of the IR receiver slightly to center it over the control panel aperture
- Add test points for fan motor parameter tuning with an oscilloscope

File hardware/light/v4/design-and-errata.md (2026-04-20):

# Minuet light accessory v4.0

**Status: UNDER DEVELOPMENT, UNTESTED**

The Minuet light accessory attaches a ring of addressable LEDs to your fan.

## Design synopsis

The [TPS22810](https://www.ti.com/lit/ds/symlink/tps22810.pdf) high side load switch supplies power to the LEDs.  It can also be used to drive other loads but it's not intended to be used for PWM.

The [SN74LVC1G17](https://www.ti.com/lit/ds/symlink/sn74lvc1g17.pdf) buffer level shifts the addressable LED data signal to 5 V.

The [LP2985-50DBVR](https://www.ti.com/lit/ds/symlink/lp2985.pdf) linear voltage regulator provides the 5 V reference for the addressable LED data signal.  It can also supply up to 150 mA for other purposes.  The voltage regulator has an extremely small quiescent current so it won't drain your battery and you can cut the `5V EN` jumper to disable it entirely if you don't need it.

The board exposes the expansion port signals and includes a small prototyping area of 0.1" (2.54 mm) pitch through-hole pads for building your own circuits based on these components.

The board gets its power from the Minuet fan controller board.  Please consider these specifications to appropriately size your loads to the available supply.

- 12 V supply is unregulated, 1 A current available
- 5 V supply is regulated, 150 mA current available.
- 3.3 V supply is regulated, 600 mA current available

[View the schematics in PDF format](light.pdf)

## Circuit board

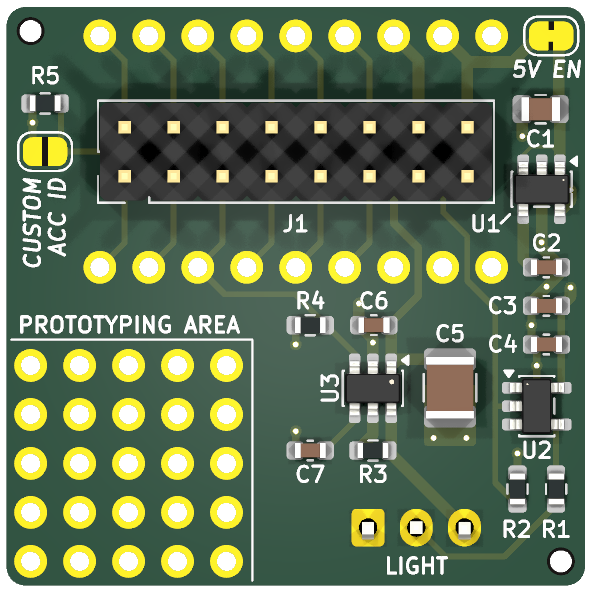
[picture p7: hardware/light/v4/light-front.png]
Front side of circuit board


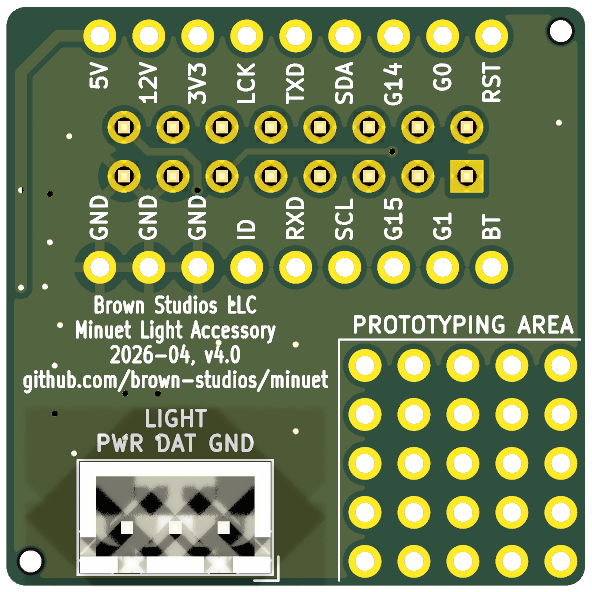
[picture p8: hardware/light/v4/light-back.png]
Back side of circuit board


## Fabrication

Use the `JLCPCB fabrication toolkit` plug-in to generate files for JLCPCB.

Fabrication parameters:

- Material: 2 layers, FR4 TG135, ENIG, 1 oz outer copper
- Via covering: tented or plugged
- Min via hole size: 0.3 mm (default)
- Board outline tolerance: 0.2 mm (default)
- PCBA type: standard or economic
- Assembly side: top and bottom, or just the top if you plan to assemble the bottom connectors manually
- Edge rails: by JLCPCB
- Tooling holes: by customer
- Parts selection: by customer
- Solder paste: high temp (default)
- Conformal coating: optional (omit if board is intended to be used for prototyping)
  - Do not spray connectors

## Installation

Make sure your addressable LED light strip is designed for 12 V and uses 3-wire signaling (WS2812B, SK6812, or similar).  The official Minuet firmware assumes an SK6812 RGBW LED strip with 57 pixels.  You may need to customize the firmware if you attach something else.

Turn off power to the fan while making these connections.

Connect the light to the [JST XH](https://www.jst.com/wp-content/uploads/2021/01/eXH-new.pdf) port labeled `LIGHT`.  Refer to the labels on the circuit board for the correct orientation.

- pin 1 labeled `GND` is ground
- pin 2 labeled `DAT` is 5 V data, controlled by `GPIO14`, 32 mA maximum output current
- pin 3 labeled `PWR` is 12 V power, controlled by `GPIO15`, 1 A maximum output current

Plug the accessory into the Minuet `EXPANSION PORT`.  Take care that the pins are aligned with the socket.

## Usage

Refer to the [user guide](../../../docs/user-guide.md) for how to operate the light accessory using the fan's keypad or an infrared remote.

## Accessory identification

By default, this circuit board identifies itself to Minuet as a "light accessory" when plugged into the expansion port.  If you repurpose this circuit board for a different function, close the `CUSTOM ACC ID` solder jumper to prevent the firmware from automatically configuring the expansion GPIOs.

Refer to the [main board design](../../minuet/v4/design-and-errata.md) for details.

## The 12 V supply is unregulated

The 12 V supply is unregulated and will reflect the voltage of whatever the fan is connected to, such as a battery whose voltage may vary by a few volts as it charges and discharges.

Typically, LED lights won't mind being driven a few volts more or less than 12 V but they will dissipate more heat at higher voltages and could potentially be damaged if operated as full brightness that way for a long time.

If you need voltage regulation for your load, consider connecting a 12 V DC buck-boost converter either upstream of the fan or downstream of the power terminal.

## How many addressable LED pixels can I use?

It depends on the LED strip that you use.  Here's some general guidance.  If you're not already familiar with addressable LEDs, we suggest looking for a more thorough tutorial.

As a rough estimate, a typical RGB LED pixel draws 0.3 W when red, green, and blue are at full brightness and a typical RGBW LED pixel draws an extra 0.1 W when the white channel is also lit at full brightness.  It adds up quickly when you multiply by the number of pixels!

In practice, you can drive a lot more LEDs if you don't run them at full brightness.  If you run them at 50% intensity, they use about 1/4 the power, they're still plenty bright, and they will last longer because they produce less waste heat.

With the available 12 W of power from the `LIGHT` connector, you should be able to light about 40 RGB pixels at full brightness and many more when operated at a reduced brightness.  Plenty for lighting up the fan cowling or part of the ceiling.

Recommendation: Use RGBW addressable LED strips with a warm white or cold white channel to improve [color rendering](https://en.wikipedia.org/wiki/Color_rendering_index) when used for white light general illumination.  Mixing RGB to produce white without a dedicated white channel makes everything look weird.

## Errata

Nothing yet...

## Changelog

Changes in v4.0:

- Replace the P-channel MOSFET output driver with a load switch.  It is more energy efficient, uses fewer components, and costs less to assemble.
- Update expansion port signals and add accessory identification resistor.
- Increase bulk capacitor physical size to compensate for DC bias derating.
- Adjust fabrication parameters: board edge clearance, silkscreen height

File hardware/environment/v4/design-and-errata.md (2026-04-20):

# Minuet environmental sensor accessory v4.0

**Status: UNDER DEVELOPMENT, UNTESTED**

The Minuet environmental sensor accessory measures CO₂, temperature, humidity, and barometric pressure.  It is designed to start the fan for ventilation when it gets stuffy inside.  An elevated CO₂ measurement often indicates inadequate ventilation in occupied spaces.

## Design synopsis

The [Sensirion STCC4 CO₂ sensor](https://sensirion.com/media/documents/6AED4B15/69295E41/CD_DS_STCC4_D1.pdf) measures the thermal conductivity of the surrounding air volume to estimate CO₂ concentration in standard atmospheric conditions.  It requires a discrete temperature and humidity sensor to operate and is designed to interface directly with SHT4x.  The sensor's self-calibration algorithm assumes it is exposed to fresh air of approximately 400 ppm atmospheric CO₂ concentration at least once a week.  See also: [STCC4 design guide](https://sensirion.com/media/documents/4B786C73/68E5EE93/CD_AN_STCC4_Design-In_Guide_D1_1.pdf).

The [Sensirion SHT40 temperature and humidity sensor](https://sensirion.com/media/documents/33FD6951/67EB9032/HT_DS_Datasheet_SHT4x_5.pdf) is connected directly to the STCC4.  Either the SHT40-AD1B or SHT41-AD1B sensors could be used for this application.  Both parts have similar typical accuracy, SHT40 is less expensive whereas SHT41 is more accurate at extreme temperature and humidity.  See also: [SHTxx handling instructions](https://sensirion.com/media/documents/6D95AA80/6840311F/HT_Handling_Instructions_SHTxx.pdf).

The [Bosch BMP580 pressure sensor](https://www.bosch-sensortec.com/media/boschsensortec/downloads/datasheets/bst-bmp581-ds004.pdf) provides barometric pressure compensation for CO₂ measurements to allow the STCC4 to operate over its full range of 70 to 110 kPa automatically.  It can also measure ambient temperature.  Either the BMP580 or BMP581 could be used for this application.  Both parts have ample accuracy for absolute pressure compensation, BMP580 is less expensive whereas BMP581 is more accurate for relative pressure measurements.

| Sensor | Typical accuracy | Recommended operating range | Maximum operating range |
| --- | --- | --- | --- |
| STCC4 CO₂ | +/- 100 ppm + 10% of reading | 10 to 40 °C, 20 to 80 %RH, 70 to 110 kPa | -40 to 85 °C, 0 to 95 %RH |
| SHT40 Temperature  | +/- 0.2 °C | 5 to 60 °C | -40 to 125 °C |
| SHT40 Humidity | +/- 1.8 %RH | 20 to 80 %RH | 0 to 100 %RH |
| BMP580 Pressure | +/- 30 Pa abs., 6 Pa rel. | 30 to 125 kPa | 30 to 125 kPa |
| BMP580 Temperature | +/- 0.5 °C | -5 to 55 °C | -40 to 85 °C |

The circuit board connects to Minuet with a QWIIC compatible I2C connector.  It can be daisy-chained with additional I2C accessories and it can also be reused with devices other than Minuet for other projects.

The Minuet thermostat can be configured to use the SHT40 or BMP580 temperature measurements although the Maxxfan's built-in thermistor does a pretty good job of measuring ambient temperature on its own.

[View the schematics in PDF format](environment.pdf)

## Circuit board

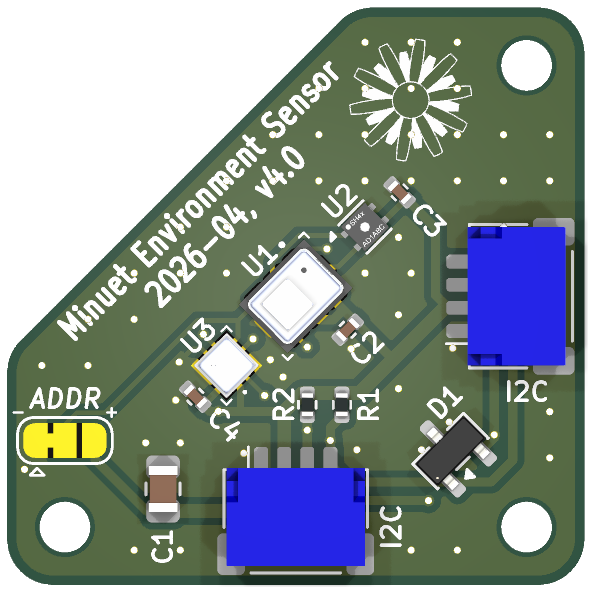
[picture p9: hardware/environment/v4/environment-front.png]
Front side of circuit board


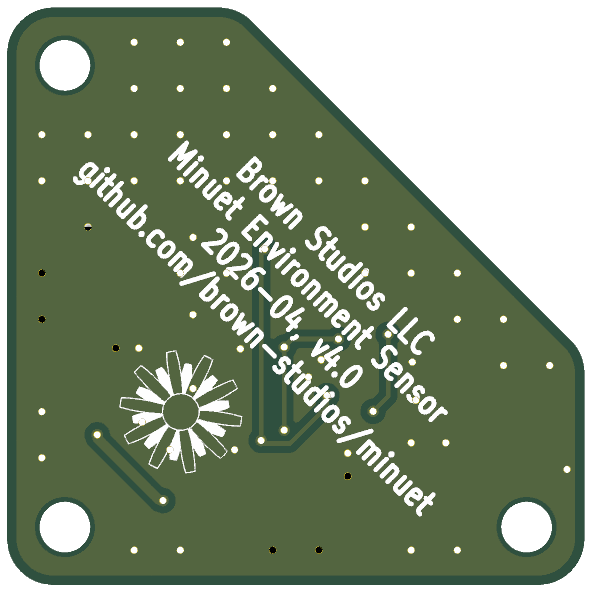
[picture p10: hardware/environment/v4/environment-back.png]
Back side of circuit board


## Fabrication

Use the `JLCPCB fabrication toolkit` plug-in to generate files for JLCPCB.

Fabrication parameters:

- Material: 4 layers, FR4 TG135, ENIG, 1 oz outer copper
- Via covering: tented or plugged
- Min via hole size: 0.3 mm (default)
- Board outline tolerance: 0.2 mm (default)
- PCBA type: standard (required to inspect placement of the LGA parts)
- Assembly side: top
- Edge rails: by JLCPCB
- Parts selection: by customer
- Solder paste: high temp (default)
- Board cleaning: no (SHT4x must not be immersed in water)

## Configuration

There are two pairs of I2C target addresses available for the sensors on the board.  To change the addresses from the default to the alternate values, cut the `ADDR` jumper trace and solder the center terminal to the `+` end of the jumper instead.  Verify your work to ensure that the `-` and `+` terminals do not short to one another.

| `ADDR` setting | STCC4 address | BMP580 address |
| --- | --- | --- |
| `-` (low / default) | 0x64 | 0x46 |
| `+` (high / alternate) | 0x65 | 0x47 |

## Installation

- Insert the circuit board into the [3D printed enclosure](https://cad.onshape.com/documents/1b4154154bb1710b0f38ccf8/w/a54da3e9e2c2de86ffdeda95/e/3829733eff25754f3b30d6cd) such that the angled face tucks under the retention lip and the pins are aligned with the mounting holes.
- Press the circuit board onto the pins until it snaps into place.
- Press the lid onto the enclosure.
- Attach a 40 cm QWIIC cable to either or both of the ports on the sensor.
- Secure the sensor to the corner of the Maxxfan front panel closest to the temperature sensor with VHB tape.
- Connect the other end of the QWIIC cable to the Minuet main circuit board.

## Usage

Refer to the [user guide](../../../docs/user-guide.md) for how to view the sensor data and configure the thermostat to use the sensors.

## Errata

Nothing yet...

## Changelog

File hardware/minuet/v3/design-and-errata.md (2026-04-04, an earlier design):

# Minuet v3.0

**Status: SUPERSEDED BY v4**

Minuet v3 upgrades the Maxxfan by replacing the circuit board.

Minuet integrates a brushless DC fan motor driver with field-oriented control optimized for quiet operation and it has a microcontroller with built-in WiFi for home automation.

## Design synopsis

The microcontroller is an [ESP32-C3](https://www.espressif.com/sites/default/files/documentation/esp32-c3-wroom-02_datasheet_en.pdf) with 4 MB of flash, a single core, and an integrated 2.4 GHz antenna.  It is ample for running ESPHome.

The fan motor driver is a [MCF8316D](https://www.ti.com/lit/ds/symlink/mcf8316d.pdf).  It supports sensorless brushless DC motors with field oriented control with current limiting, built-in motor parameter estimation, and I2C interface.  The integrated buck converter is disabled as per this [application note](https://www.ti.com/lit/an/slla643/slla643.pdf).

The lid motor driver is a [DRV8876](https://www.ti.com/lit/ds/symlink/drv8876.pdf).  It has built-in current limiting which is used to detect stalls at the end-of-travel when the lid is completely opened or closed.

The [TCA9555](https://www.ti.com/lit/ds/symlink/tca9555.pdf) IO expander on-board provies an 16 additional IO pins with built-in pull-up resistors via I2C.

The [TPS561201](https://www.ti.com/lit/ds/symlink/tps561201.pdf) buck converter supplies 1 A at 3.3 V.  It is optimized for high efficiency at low current consumption to minimize vampire drain while the fan is turned off and the ESP32-C3 is in a low power state.

The [TSOP39238](https://www.vishay.com/docs/82778/tsop392.pdf) IR receiver supports the Maxxfan IR remote control.

The `EXPANSION` port enables accessories and factory programming.  It exposes four free GPIO pins that can be used for any purpose, the serial port, the I2C bus, the safely lock signal, the reset and bootloader signals, and the 3.3 V and 12 V power rails.  For example, with just a few components you could use the GPIO expansion port to attach an addressable LED strip for fancy lighting around the fan enclosure.

The `QWIIC` port allows readily available I2C accessories (such as environmental sensors) to be connected with ease.

The `TEMP` port connects to the Maxxfan's built-in thermistor for use by the automatic thermostat.

The `RAIN` port connects to the Maxxfan's rain sensor (only certain models).  It has a high impedance input and uses a comparator to detect a small current flowing through water on the sensor.

The `LOCK` port triggers a safety lock function that stops the fan, closes the lid, and inhibits operation.

The USB-C port and the `BOOT` and `RESET` tactile switches are used for accessing the bootloader and programming the firmware.

A simple voltage divider measures the supply voltage and triggers a software-controlled low battery protection function.

A piezo buzzer provides audible feedback.  Minuet aims to be polite about its use of audible feedback.  It can be configured in software or disabled in hardware by cutting a jumper trace.

[View the schematics in PDF format](minuet.pdf)

## Circuit board

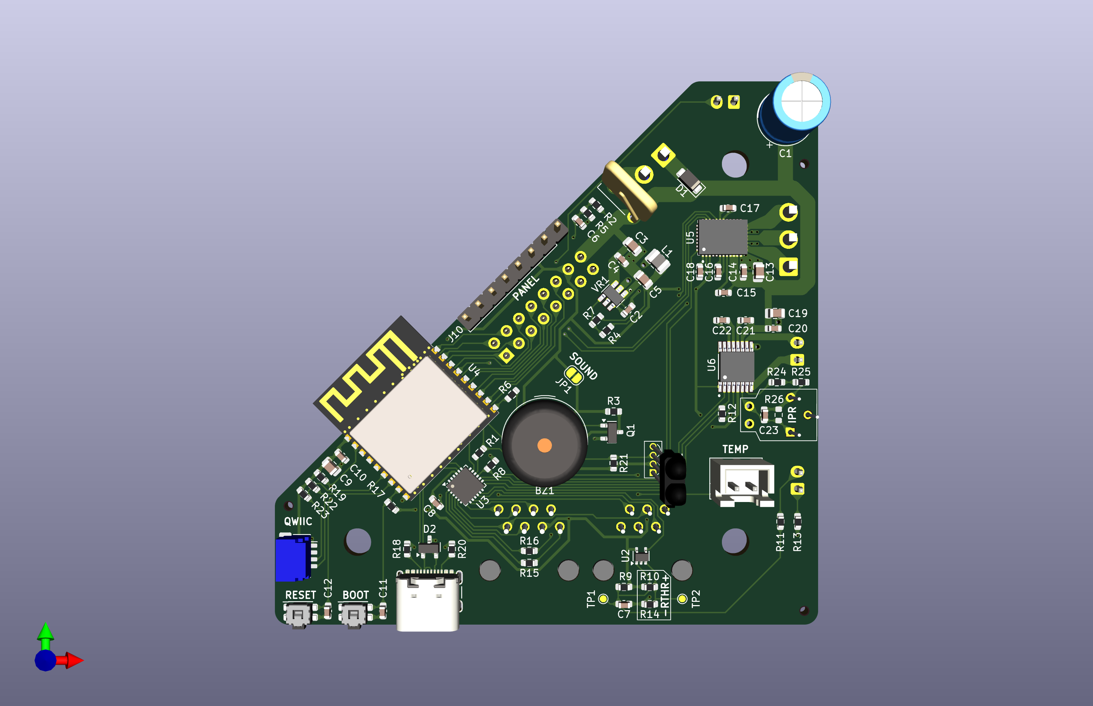
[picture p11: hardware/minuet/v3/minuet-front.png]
Front side of circuit board


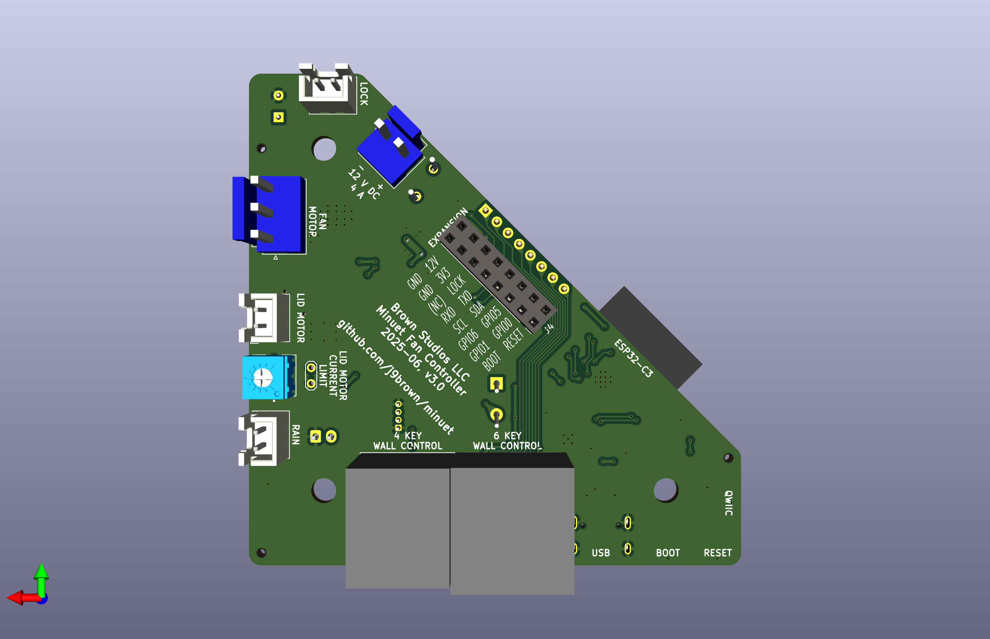
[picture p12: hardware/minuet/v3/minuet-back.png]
Back side of circuit board


## Recommended operational parameters

Recommended electrical supply specifications:

- Voltage: 12 V DC nominal and absolute maximum range from 9 to 16 V DC
- Wiring: minimum 18 AWG (0.8 mm²)
- Circuit protection: 5 A fuse or circuit breaker

Recommended motor specifications:

- Fan motor: Brushless DC motor rated for the supply voltage and constant operation, no hall sensors needed, driven with up to 4 A current per phase
- Lid motor: Brushed DC motor rated for the supply voltage and intermittent operation, can draw up to 2 A current

Please test your set up carefully and monitor heat dissipation if you choose to operate Minuet beyond these recommendations.

## PCB assembly

The KiCad project contains the bill of materials.  It includes part numbers and orientations of all SMT components for the JLCPCB PCBA service.

You will need advanced soldering skills to completely assemble this project by hand.  Although most of the components can be soldered by hand, a few parts have very fine pitch pads that are inaccessible from the sides.  You will need a solder stencil, fine solder paste, and a temperature controlled hot plate or a reflow oven.  The fan motor driver chip in particular must be carefully soldered to ensure an efficient thermal bond to the PCB.  You may find it easier to buy a board with the SMT components pre-assembled and then solder the remaining through-hole components by hand.  The IR receiver cannot be installed at the factory because it requires a standoff.

All of the SMT components are on the front side of the board.  They should be soldered first before moving on to the through hole components.

There are through hole components on both sides of the board.  Follow the silkscreen courtyard markings to determine the correct orientation.  Be aware that labels for connectors appear on both sides of the board.

The 1x8 pin header labeled `PANEL` must have a sufficient mating contact length to securely attach the keypad's flex connector.  The BOM specifies a part with an 8.1 mm mating contact length that works well.  Shorter contacts may be fine but the connector could come loose under vibration so be sure to check the fit.

The IR receiver must be raised above the board as far as the leads can be extended (about 16 mm) to be visible through the clear window in the keypad.  Thus the IR receiver will need mechanical support to keep it propped up and to insulate the leads.  You can 3D print a suitable standoff from [this model](https://cad.onshape.com/documents/11f07c0bb608e7010778ac35/w/a82f75dceda39e564795dbd4/e/5949b73994c9747af7d1d4c9) or make your own using other materials such as cardboard.

There are test points on the board near the lid motor current limit trim potentiometer to help you measure the resistance as you make adjustments.

You can safely omit certain components that you don't need including the IR receiver, the 6P6C and 8P8C connectors for wired wall controls, the rain sensor circuitry, the buzzer, and the current limit trim potentiometer (if you add a fixed resistor instead).

To improve the circuit board's moisture resistance, you can spray it with an insulative conformal coating after taking care to mask off all connectors before spraying so they don't get coated unintentionally.

## Setup

### Temperature sensor

Connect the Maxxfan's temperature sensor to the `TEMP` port.  You can make your own temperature sensor connecting any 10 Kohm NTC thermistor to a JST XH-2 plug in any orientation.  Update the thermistor beta constant in the firmware to ensure accurate readings.

The temperature sensor is driven by an IO pin to minimize resistive self-heating and power usage between samples.  The Maxxfan's built-in thermistor appears to have a beta constant of 3950.

### Rain sensor

Connect the Maxxfan's rain sensor to the `RAIN` port.  You can make your own rain sensor by mounting two wires to a surface that's exposed to the rain such that water will form a conductive path between them.  Connect the wires to a JST XH-2 plug in any orientation.

The rain sensor circuit uses a comparator to detect a small current flowing between bare electrodes immersed in water.  The circuit has high impedance to protect itself from the environment especially because it is DC coupled to the sensing electrodes (just like the original equipment).

You can omit the comparator and other rain sensor components if you don't need the rain sensor.  Alternatively, you could repurpose the `RAIN` port for a button input or conductive touch sensor.

In a subsequent revision, it might be interesting to explore AC coupling the rain sensor to improve isolation or removing the comparator to reduce the BOM.

### Safety lock

Connect a switch to the `LOCK` port with a JST XH-2 plug to trigger a safety lock function that that stops the fan, closes the lid, and inhibits operation.  You can connect several switches in parallel to inhibit operation under a multitude of external conditions.

Here are some suggested applications:

- Attach a magnet to your insulated vent cover and a normally-open reed switch connected to the `LOCK` port somewhere in the fan trim ring or ceiling to inhibit operation while the insulated vent cover is installed.
- Connect a relay or optocoupler to inhibit operation of the fan while the engine is running.

Pin 1 is ground.  Pin 2 is a digital input with a pull-up to 3.3 V.  The safety lock engages when pin 2 is low (tied to ground) and disengages when pin 2 is floating.

### Piezo buzzer

The piezo buzzer is designed with politeness in mind which may be a matter of personal preference.

You can customize or disable the sounds it makes in software.

You can disable the buzzer altogether in hardware by cutting the `SOUND` jumper trace on the board.  Alternatively, if you want to make the buzzer louder, then you can cut the jumper and solder a wire from the buzzer side of the `SOUND` jumper to the 12 V bus.

And if you want to make the fan play a cheerful jingle any time it turns on then you can change the firmware to do that with [RTTTL](https://en.wikipedia.org/wiki/Ring_Tone_Text_Transfer_Language).

### Fan motor

Connect a suitably rated brushless motor to the `FAN MOTOR` port with a JST VH-3 plug.  Pin 1 is phase A, pin 2 is phase B, pin 3 is phase C.  If the motor operates in the reverse direction than you expect, simply swap any two phases.

Configure the motor parameters in the software.

The [MCF8316D](https://www.ti.com/lit/ds/symlink/mcf8316d.pdf)] is configured to mostly be controlled and monitored over I2C instead of spending precious GPIOs on control signals.  The buck converter is disabled because it isn't needed.  This board is not compatible with any other versions of the MCF8316.

### Lid motor

Connect the Maxxfan's lid motor to the `LID MOTOR` port with a JST XH-2 plug.

Minuet detects when the lid motor has reached the end of its travel when opening or closing the lid when the lid motor driver reports an overcurrent fault or after a fixed duration of time has elapsed.

The lid motor current limit must be set high enough to ensure that the motor has enough torque to overcome the friction of the lift mechanism.  And ideally it should be low enough to reliably detect the lid motor stall at end of travel.  The safe default current limit ensures sufficient torque for sticky motors but it may cause Minuet to wait until the timeout to report the completion of lid motor travel.

If your lid does not open or close fully, try increasing the lid motor current limit a little bit.  Or if your lid motor moves freely, you can try reducing the default to more reliably detect end of travel.

The `IPROPI` pads set the current limit either using a fixed resistor or a 5 Kohm variable resistor.  To set this value, measure the resistance across the variable resistor at the test point near `IPROPI` and turn the potentiometer until you obtain the desired setpoint.

Formulas to calculate the current limit where `RV` is the value of the `IPROPI` resistor in ohms.

- Itrip = 1000 * 3.3 V / RV
- RV = 1000 * 3.3 V / Itrip

**Safe default: RV = 2.21 Kohms, Itrip = 1.5 A**
**Recommended setting: RV = 2.80 Kohms, Itrip = 1.18 A**

The [DRV8876](https://www.ti.com/lit/ds/symlink/drv8876.pdf) data sheet recommends adding a small value capacitor such as 10 nF to `IPROPI` to reduce glitches if faults are detected prematurely.  It might be possible to adjust the value of this capacitor to a larger value to delay premature faults for a sticky motor that needs more current to get moving.  Alternatively, `IMODE` could be configured to apply fixed off-time current chopping (but it will prevent end of travel detection).

### Expansion port

Connect Minuet accessories to the `EXPANSION` header.

And you can make your own accessories too!

The `EXPANSION` header includes the following signals.  Refer to the Minuet schematics or the board silkscreen for the complete pinout.

- `GPIO0`, `GPIO1`, `GPIO5`, `GPIO7` (was `GPIO6` in v3.0) can be used for any purpose
- `UART_RXD` and `UART_TXD` provide the serial port
- `SCL` and `SDA` provide the I2C bus (QWIIC)
- `RESET` and `BOOT` are wired in parallel with their corresponding buttons (active low)
- `LOCK` engages the safety lock (active low)
- 12 V supply is unregulated, 1 A current available
- 3.3 V supply is regulated, 600 mA current available
- Ground

The accessory PCB should be no larger than 30 mm x 30 mm to ensure it fits within the housing.  It has a 16-pin 2-row pin header with 2.54 mm pitch centered 7.5 mm from the upper edge edge.  Refer to the [light accessory](../../light) as an example for the connector placement and PCB layout.

One pin on the expansion port is not connected to anything and it is labeled *(NC)* on the silkscreen.  This pin might be used for something in a future version of Minuet so please don't connect anything to it.

### QWIIC port

Connect [QWIIC](https://www.sparkfun.com/qwiic) peripherals to the `QWIIC` port, such as environmental sensors, to this port.

## IO pins

The ESP32-C3 microcontroller has relatively few GPIOs so they are assigned to components that need specific functions first and the remaining pins are assigned to the expansion port.

- `GPIO0` & `GPIO1`: Reserved for the GPIO expansion port (IO, ADC, LEDC PWM, 32 kHz XTAL, and more functions)
- `GPIO2`: IR receiver (RMT function), strapping pin
- `GPIO3`: Voltage sensor (ADC function)
- `GPIO4`: Thermistor (ADC function)
- `GPIO5`: Reserved for the GPIO expansion port (IO, LEDC PWM, and more functions)
- `GPIO6` (was `GPIO7` in v3.0): I2C SDA
- `GPIO7` (was `GPIO6` in v3.0): Reserved for the GPIO expansion port (IO, LEDC PWM, and more functions)
- `GPIO8`: I2C SCL, strapping pin
- `GPIO9`: BOOT button, strapping pin
- `GPIO10`: Buzzer (LEDC PWM function)
- `GPIO18` & `GPIO19`: USB full-speed transceiver
- `GPIO20` & `GPIO21`: Serial port UART

The TCA9555 IO expander handles the remaining low speed digital logic functions.  These pins are designated `XIO` on the schematic.  All of the `XIO` pins have been assigned to peripherals.  Refer to the schematics for details.

## Changes from v2

- New BLDC fan motor driver with field-oriented control optimized for quiet operation
  - All fan motor parameters are programmed in software via I2C; no more jumpers
  - Works with sensorless BLDC motors
  - Directly governs the fan rotor speed (instead of the motor duty cycle as before)
- Added a safely lock signal to stop the fan, close the lid, and inhibit operation
  - When paired with a normally-open reed switch, Minuet can detect when an insulated vent cover is installed and engage the safety lock until it is removed
- Optimized the bill of materials for fabrication by JLCPCB PCBA
- Marked the schematic with the voltage ratings of the actual parts instead of the minimum necessary
- Improved the left-to-right reading order of the schematic
- Moved all of the components except some connectors and the trim pot to the front side of the board to best take advantage of LCSC single-sided economic PCBA although it would perhaps be better to keep the PTC fuse on the back side (facing up when installed) for improved free air convection

## Errata

Issues in v3.0:

- There should be a 1 uF capacitor from FB_BK to GND_BK according to the MCF8316D datasheet (although it works fine without it).
- Should add motor phase labels to the silkscreen for clarity and relabel all of the documentation to A/B/C to match the data sheet.
- The rain sensor does not work.  The Minuet v3.0 boards were assembled with LMV331IDCK which has a PNP input stage and only allows a common mode input voltage up to Vcc - 0.7 V = 2.6 V whereas the actual signals are in the range of 3.1 V.  The Minuet v2.* boards used LMV331X which has no such limitation and worked as expected (but this part was not available at JLCPCB).  Suitable rail-to-rail alternatives: TL331LV, TLV7041, TLV7021.
- Some areas of the PCB reach over 50 C when operating the motor at 4 A peak per phase.  At 4.5 A, we can see over-temperature warnings.  Consider adding a copper pour to the front layer with thermal vias.
- The bootloader enables the GPIO6 pull-up on reset which interferes with its use for the Minuet light accessory board and causes the LED strip to be powered on prematurely.  Should swap GPIO6 and GPIO7 (SDA) because we need the pull-up on SDA anyhow.  Workaround by setting EFUSE_DIS_PAD_JTAG = 1.

    `espefuse.py --chip esp32c3 --port /dev/tty.usbmodem11201 burn_efuse DIS_PAD_JTAG`

- The 3D model for the IR receiver should have a 16 mm standoff, currently it's set to 17 mm
- The lid motor end of travel detection does not work reliably because the current limit is too sensitive.  There needs to be a delay to allow for the inrush current to settle before determining that the motor has stalled.  This problem could be solved by enabling fixed off-time current chopping and checking whether V(propi) has been above a certain threshold for a certain amount of time using an ADC or comparator.  Or by providing a PWM signal to the control inputs, the cycle-by-cycle current chopping could be allowed to proceed as intended and the motor stall can be detected when NFAULT remains asserted for a long enough duration.  Or perhaps a different motor driver chip with integrated stall detection such as the DRV8235 could be used.
- The microcontroller spontaneously resets with no logs or crash data when a devices connects to the WiFi in access point mode.  The debug component reports the reset reason as a "power-on event".  The 3.3 V supply does not show any transients during the event so the problem appears to be internal to the ESP32-C3 module.  Reducing the WiFi output power to 19 dB resolves the issue: recommend using 18 dB for a safety margin with this version of the board.

Issues with the MCF8316D motor driver chip:

- Activating the brake function while the I2C watchdog timer is enabled causes a spurious watchdog timeout and does not brake.  Texas Instruments has [acknowledged the issue](https://e2e.ti.com/support/motor-drivers-group/motor-drivers/f/motor-drivers-forum/1555307/mcf8316d-brake-triggers-watchdog_fault-when-watchdog-is-enabled/5991916) and there is no workaround available except to disable the I2C watchdog.  Fortunately, Minuet doesn't absolutely need the brake function although it would help to stop the fan faster.

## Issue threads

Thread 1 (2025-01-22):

Minuet

wingspinner, 2025-01-22:
Hello,
Noble cause. Been mulling around designing the same thing for some time since the factory controller leaves a lot to be desired.

Big question is what is your plan on the firmware?

On the motor my calculations are the existing motor is about 60w. Anything less than that and you won't get enough air volume. Therefore you need a driver that will drive 5 amps plus safety margin. That's one of the problems with the existing controller - burns out driver FETs occasionally and the lid motor draws a little less than 2 amps and it frequently frys the too-small driver chip. Also, it needs current sensing on the lid motor so the controller can tell it when to stop.

Cheers,
Ron

j9brown, 2025-01-22:
Hi Ron,
Thanks for your interest!

The firmware is based on ESPHome and is very easy to customize (or replace with something else if desired).  You can read more about the firmware here: https://github.com/j9brown/minuet/blob/main/docs/setup-guide.md#firmware

I don't think the original fan motor is meant to run at 60 W (at least not for long).  That would be 5 A at 12 V whereas the instruction manual specifies a 5 A fuse for the circuit and the original circuit board has a 4 A PTC fuse built-in.  If you're curious, perhaps you can try measuring the current of your unmodified fan when running at full speed (with no windows open for maximum back-pressure).

By way of comparison, I tested a 50 W brushless motor at the workbench with the fan blade attached and it felt kind of scary when operated beyond about 35 W at well over 1000 RPM.  Granted there was no back pressure for the fan to struggle against in this test but I can't really imagine needing more power than that whirlwind.  I'll know more once I've completed the second revision.

The initial prototype uses a DRV10970 motor driver which has a 1.5 A current limit (18 W at 12 V).  It moves enough air for everyday use but more is needed to match the performance of an unmodified fan.  The second revision will use MCT8315Z to allow up to 3 or 4 A (36 to 48 W) which ought to be plenty.  I guess we'll find out!

As for the cover motor, Minuet uses a DRV8876 motor driver with built-in current limiting set to about 1.2 A.  When the cover reaches end-of-travel, the motor stalls, and the driver automatically cuts power to the motor and signals the firmware.  It works well!  This driver chip is rated for 3.5 A so with any luck it won't burn out prematurely.

What else would you like to know?
Jeff.

j9brown, 2025-01-23:
*nod* We'll need to conduct further experiments to determine the appropriate fan motor size.  It helps that brushless motors tend to be more efficient than brushless ones and that electronic commutation does not generate arcs and current spikes that might otherwise prematurely damage the driver.  As you point out, we do need to take into account heat dissipation to achieve the hoped for power handling.

It sounds like your lid motor might be a little stickier than mine.  Fortunately, adjusting the current limit is just a matter of changing out a single resistor.  DRV8876 is rated for upwards of 3 A which is ample, especially given that the lid motor only operates for a few seconds at a time.

Using a half-bridge driver with discrete FETs sounds like a good idea to increase current handling capacity when you need it.  There seem to be some off-the-shelf dev boards with these parts that would be useful for prototyping.

The Minuet firmware is entirely open source.  It's based on the [ESPHome](https://esphome.io/) platform.  It has a large active community of developers with a monthly release cadence and is funded by the Open Home Foundation.  The configuration files for Minuet are already [here in this repository](https://github.com/j9brown/minuet/blob/main/esphome) and that's all you need to build the firmware.

It sounds like you had fun swapping out the microcontroller!  I'm curious how you decided to customize the behavior of the fan for your needs.  Did you make any changes to the control scheme?  What have you connected to it over WiFi?

Closed 2025-02-23.

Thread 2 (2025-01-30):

Let use configure the behavior on power-on and low-battery

j9brown, 2025-01-30:
Requested [here](https://sprinter-source.com/forums/index.php?threads/137317/page-2#post-1669596)

Ideas:
- Add settings for the power-on and restore from low-battery behavior: leave fan off and ensure cover closed, leave fan off and leave cover in prior state, restore fan speed and prior cover state, restore fan and cover to some preset initial state
- Add settings for the voltage threshold for low-battery detection
- Add settings for the low-battery behavior: turn off fan and leave cover open or close it

The stored cover state can get out of sync if the user turns the knob manually.  Could possibly add code to synchronize the cover state by closing the clover and detecting whether the motor stalls immediately (meaning the cover was already closed) or if it took a little while to stall (meaning it was previously open).  If done on power-on, then we could add another option for restore behavior where the fan speed is restored only if the cover was not manually closed in the meantime.

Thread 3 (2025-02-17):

Let users disable wifi from within the standalone out-of-the-box experience

j9brown, 2025-02-17:
Turning off wifi may save power for those who don't need it.  There should be a way to toggle wifi off and on again with a button press (preferably without needing to flash new firmware or factory reset).

Wifi disabled should perhaps be the default mode given that the Minuet AP may be vulnerable after a factory reset if the password isn't changed.  Easy enough to store the wifi enable state in flash.  Perhaps the standalone configuration initializes it to false and the integrated configuration initializes it to true.

j9brown, 2025-08-29:
Wifi is disabled by default and can be enabled from the keypad for setup.

Closed 2025-08-29.

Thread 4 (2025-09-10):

Feature request: Synchronize two Minuet fans

j9brown, 2025-09-10:
Let the user pair two Minuet fans together to coordinate their behavior.

Some examples:

- When one fan is running as an intake, the other fan runs as an exhaust at the same speed.
- When one fan is running, the other fan lid opens to passively vent and balance the interior air pressure.
- Both fans run in the same mode together.
- Synchronize the thermostat and use the same temperature reading to govern both fans.
- Synchronize the light accessory state.
- When a safety lock is engaged on one fan, either the other fan is also locked or it still operates independently

Consider using ESP-Now or Bluetooth LE to let the fans communicate.

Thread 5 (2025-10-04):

Feature Request: Support Higher Voltages

crbn60, 2025-10-04:
Many systems are now being built with 24V or 48V house voltages and supporting these would  be helpful.

j9brown, 2025-10-06:
Thanks for your suggestion!

Unfortunately, supporting higher supply voltages across such a large operating range would require replacing many of the electronic components on the circuit board.  The fan motor, lid motor, and accessory lights are designed for 12 V nominal too.

I anticipate that most folks who are upgrading their Maxxfan with Minuet on a 24 V or 48 V system will already have installed a DC-DC converter to provide a 12 V supply for their Maxxfan as required by the original equipment.  So that will work with Minuet too.

Closed 2025-10-06.

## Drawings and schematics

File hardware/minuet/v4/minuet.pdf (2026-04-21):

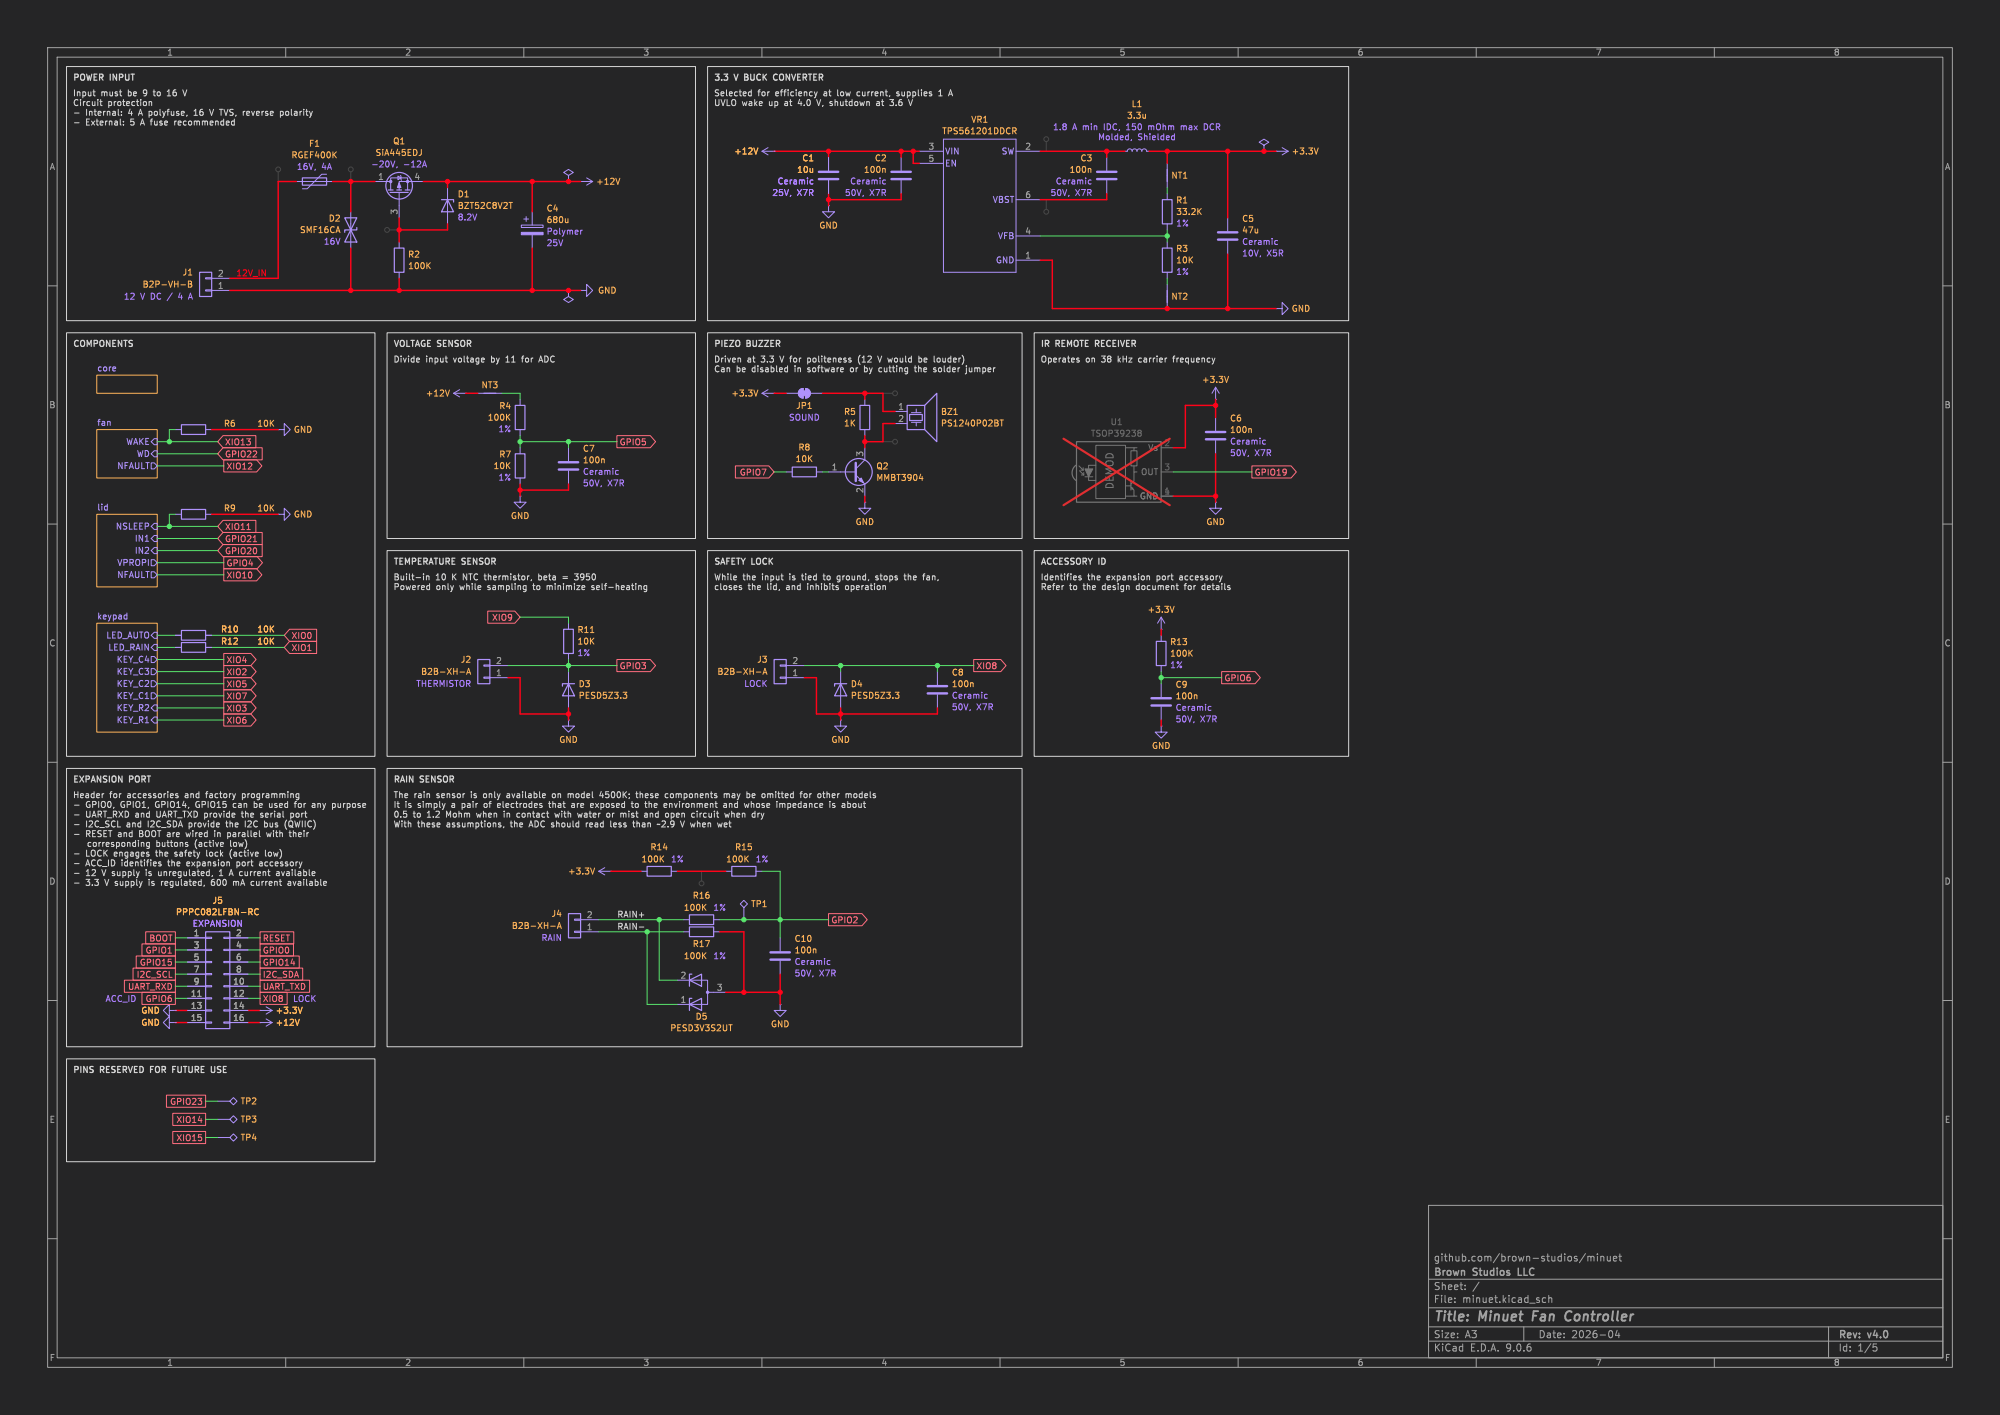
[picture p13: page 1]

Input must be 9 to 16 V Circuit protection

COMPONENTS
keypad WAKE NFAULT WD

VOLTAGE SENSOR
Divide input voltage by 11 for ADC

Operates on 38 kHz carrier frequency PIEZO BUZZER

- GPIO0, GPIO1, GPIO14, GPIO15 can be used for any purpose
- UART_RXD and UART_TXD provide the serial port - I2C_SCL and I2C_SDA provide the I2C bus (QWIIC)

- LOCK engages the safety lock (active low)

PINS RESERVED FOR FUTURE USE

github.com/brown-studios/minuet

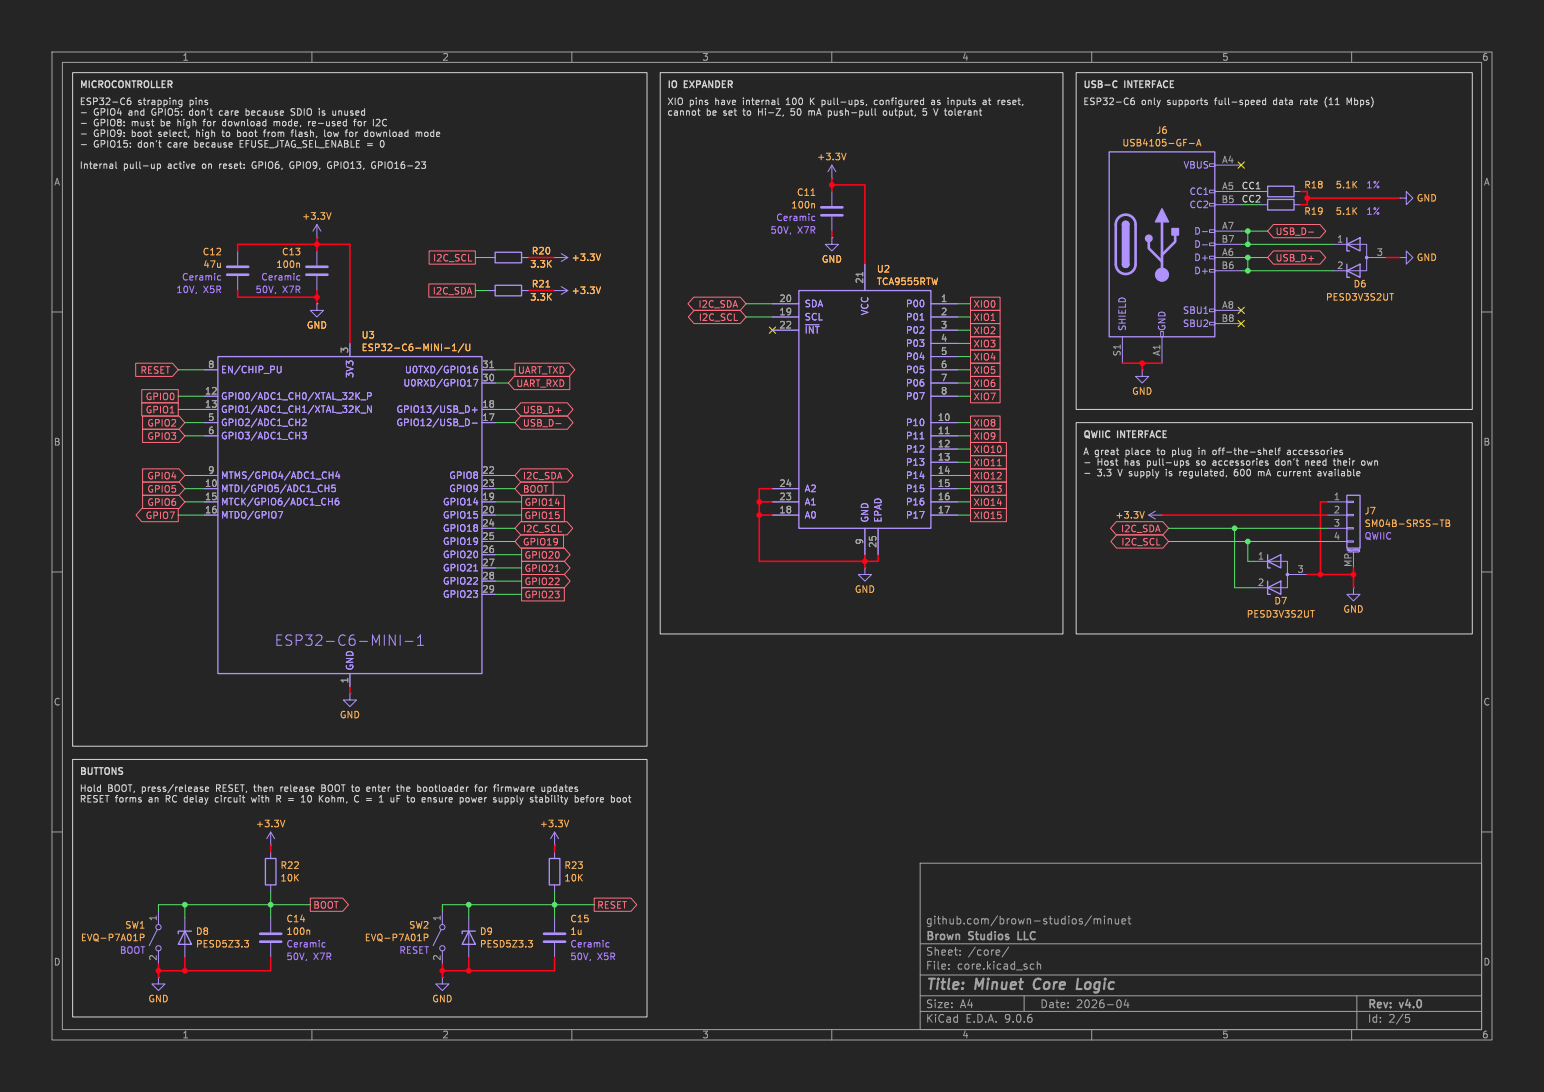
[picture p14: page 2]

- GPIO4 and GPIO5: don't care because SDIO is unused
- GPIO15: don't care because EFUSE_JTAG_SEL_ENABLE = 0

github.com/brown-studios/minuet

Id: 2/5 Title: Minuet Core Logic

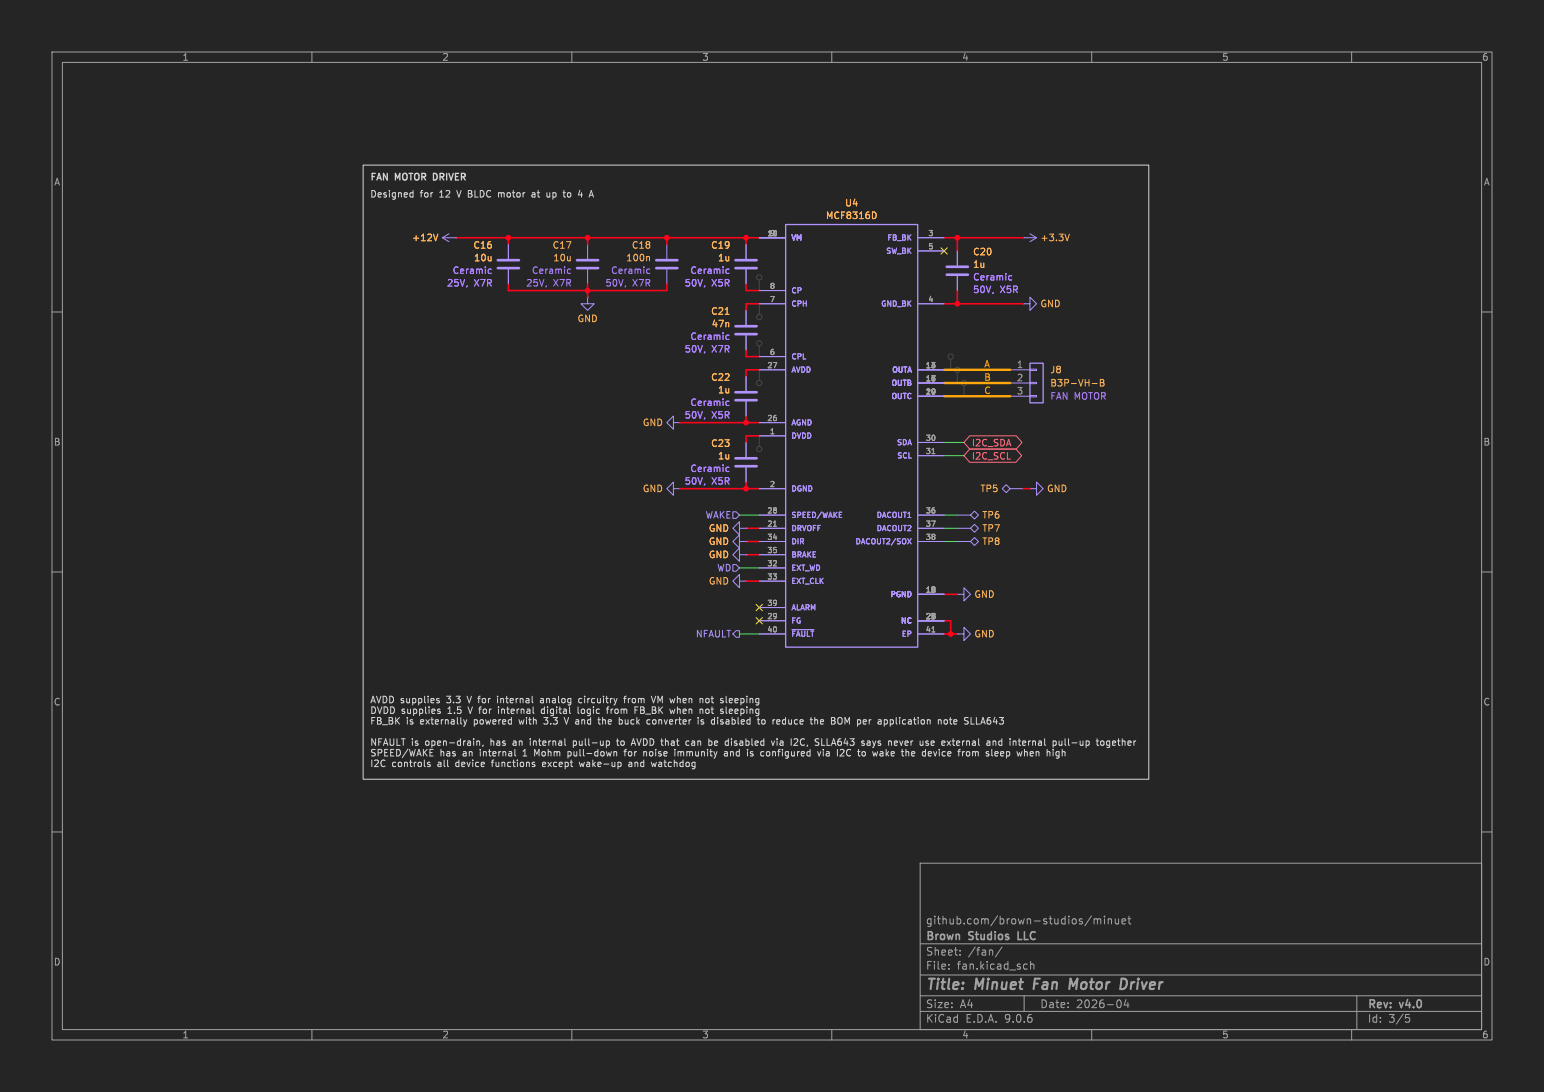
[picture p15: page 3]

FAN MOTOR DRIVER
Designed for 12 V BLDC motor at up to 4 A

U4 MCF8316D
FAN MOTOR GND GND

github.com/brown-studios/minuet GND

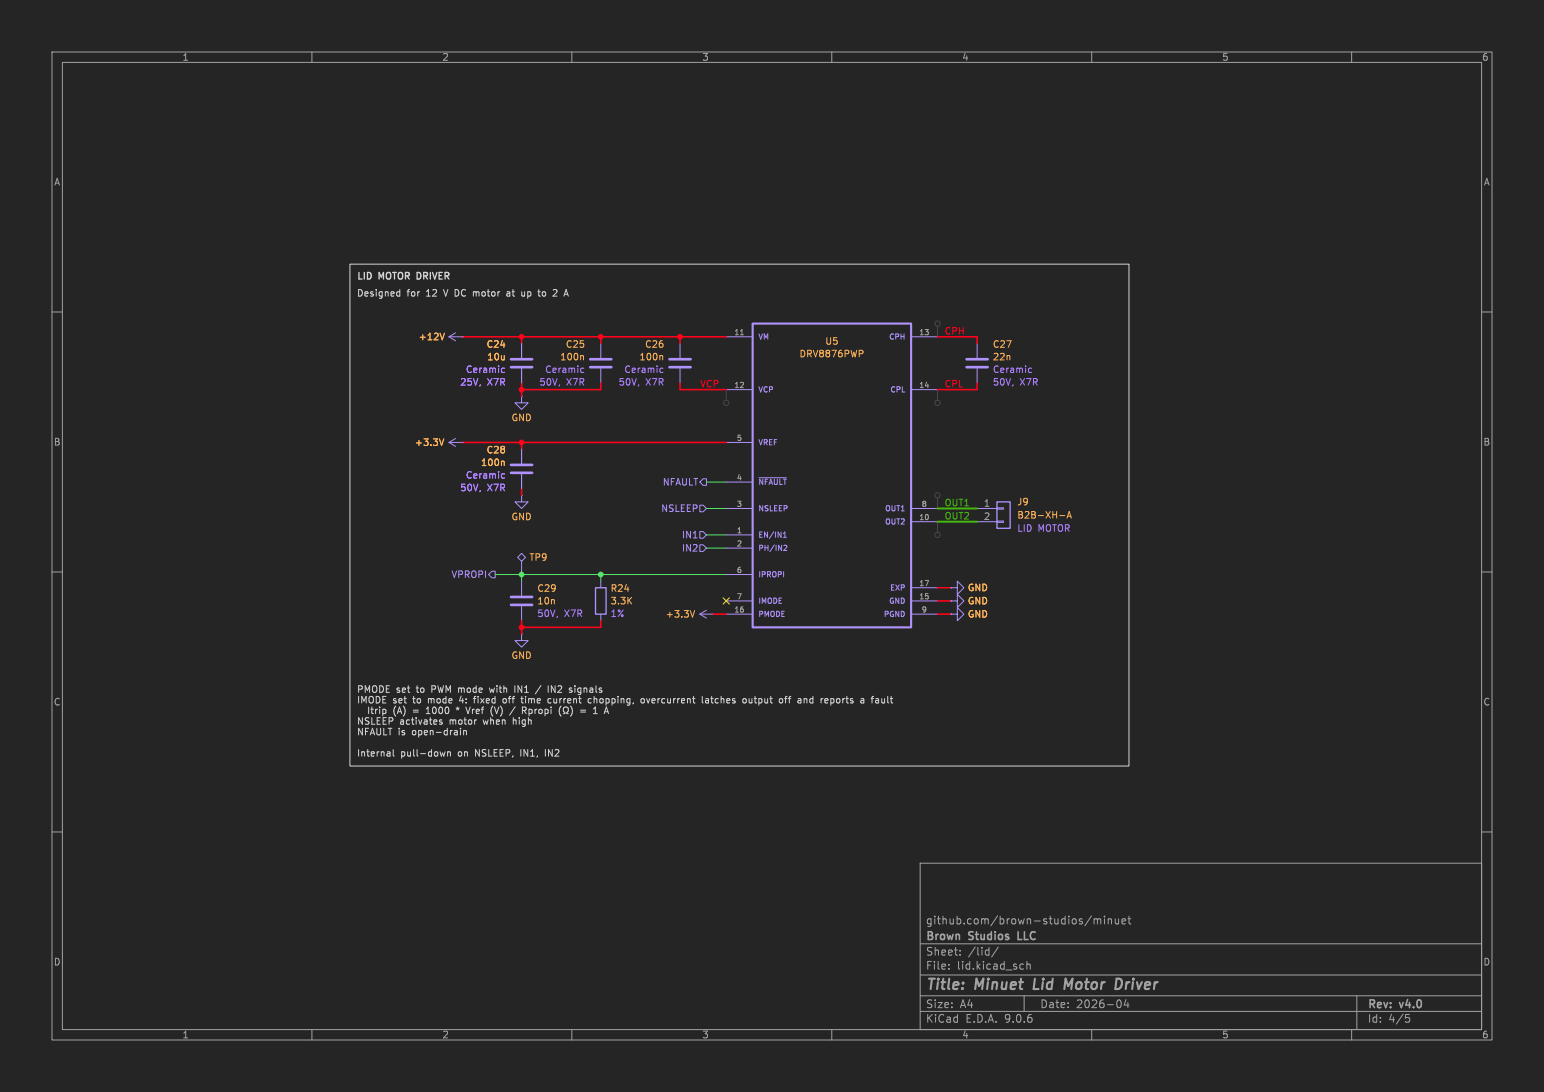
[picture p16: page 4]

LID MOTOR DRIVER
Designed for 12 V DC motor at up to 2 A

100n Ceramic 50V, X7R
github.com/brown-studios/minuet GND GND GND

PMODE set to PWM mode with IN1 / IN2 signals

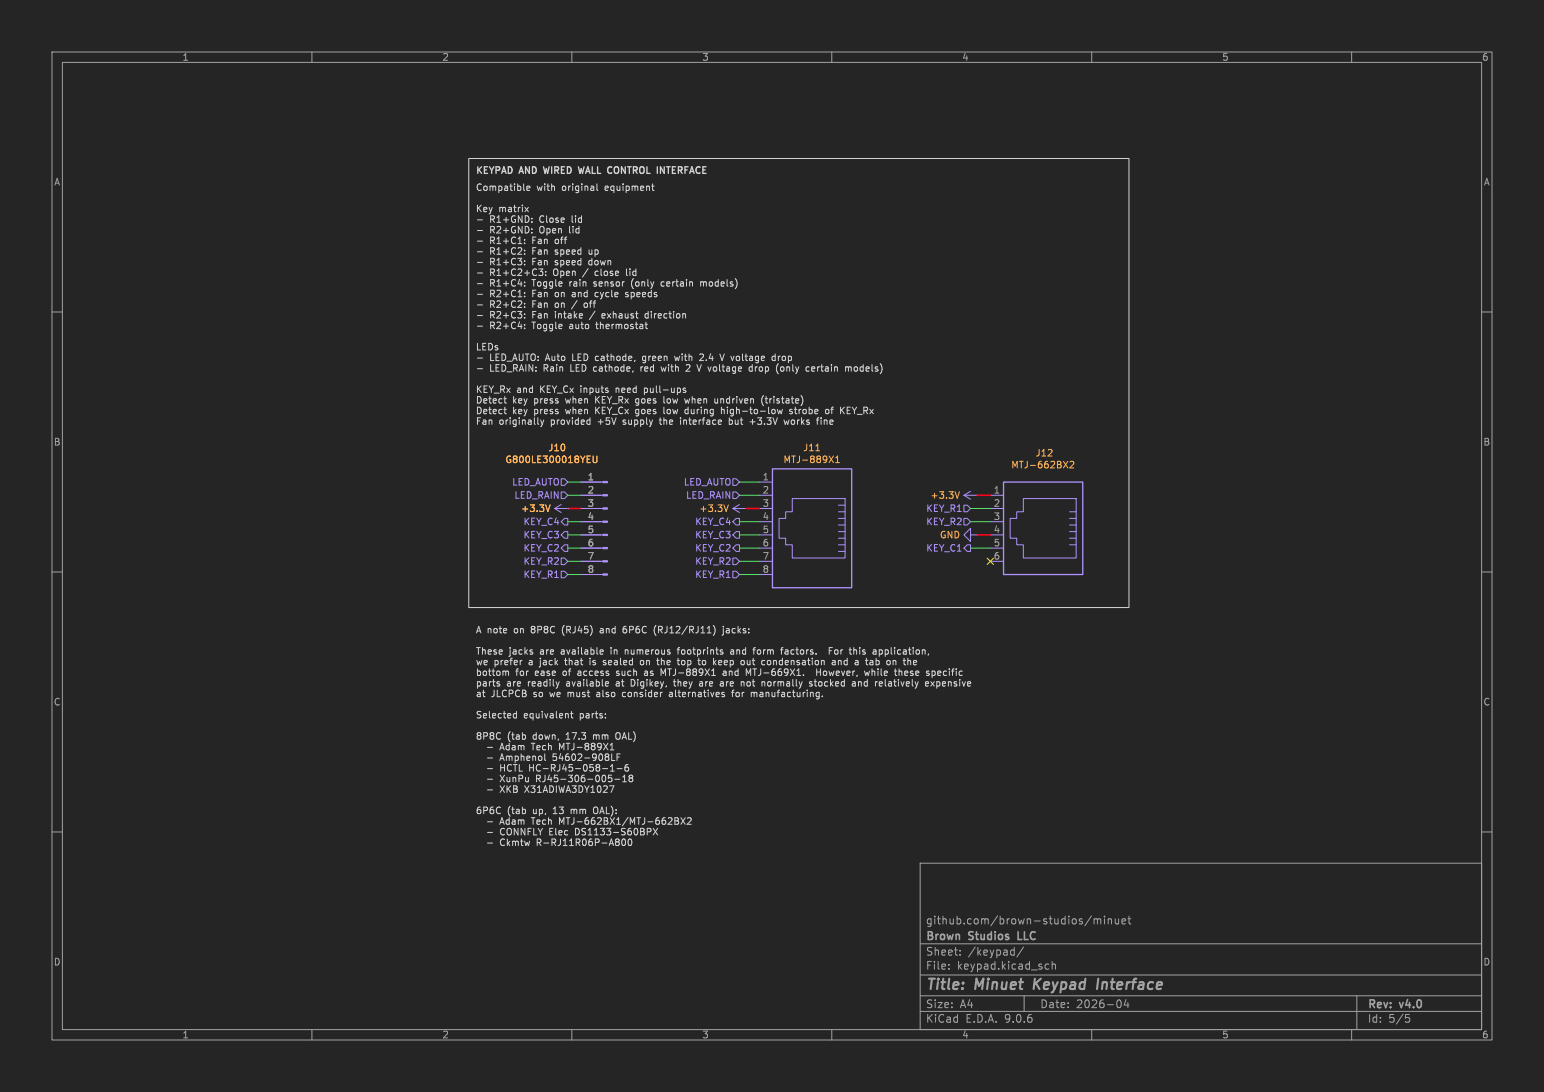
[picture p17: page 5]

6P6C (tab up, 13 mm OAL): - Adam Tech MTJ-662BX1/MTJ-662BX2 - CONNFLY Elec DS1133-S60BPX - Ckmtw R-RJ11R06P-A800

github.com/brown-studios/minuet

Id: 5/5 Title: Minuet Keypad Interface

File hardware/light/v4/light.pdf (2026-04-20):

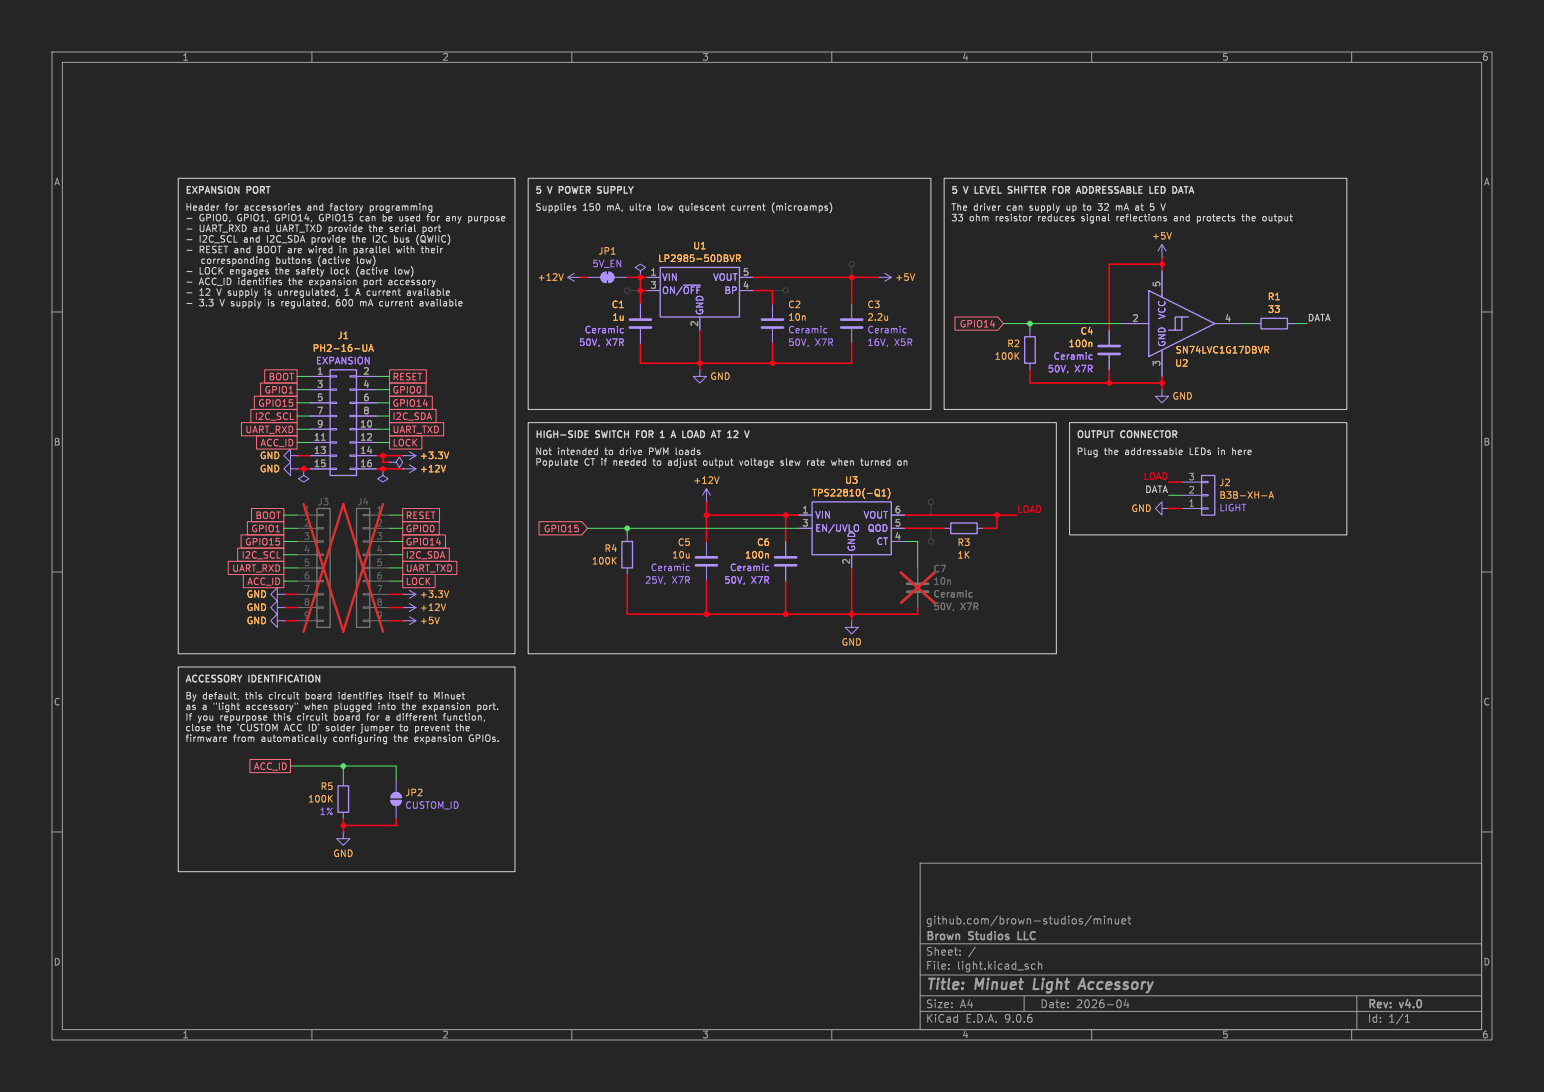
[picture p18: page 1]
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

The driver can supply up to 32 mA at 5 V

- LOCK engages the safety lock (active low)

100n Ceramic 50V, X7R GND GND GND

github.com/brown-studios/minuet

Id: 1/1 Title: Minuet Light Accessory

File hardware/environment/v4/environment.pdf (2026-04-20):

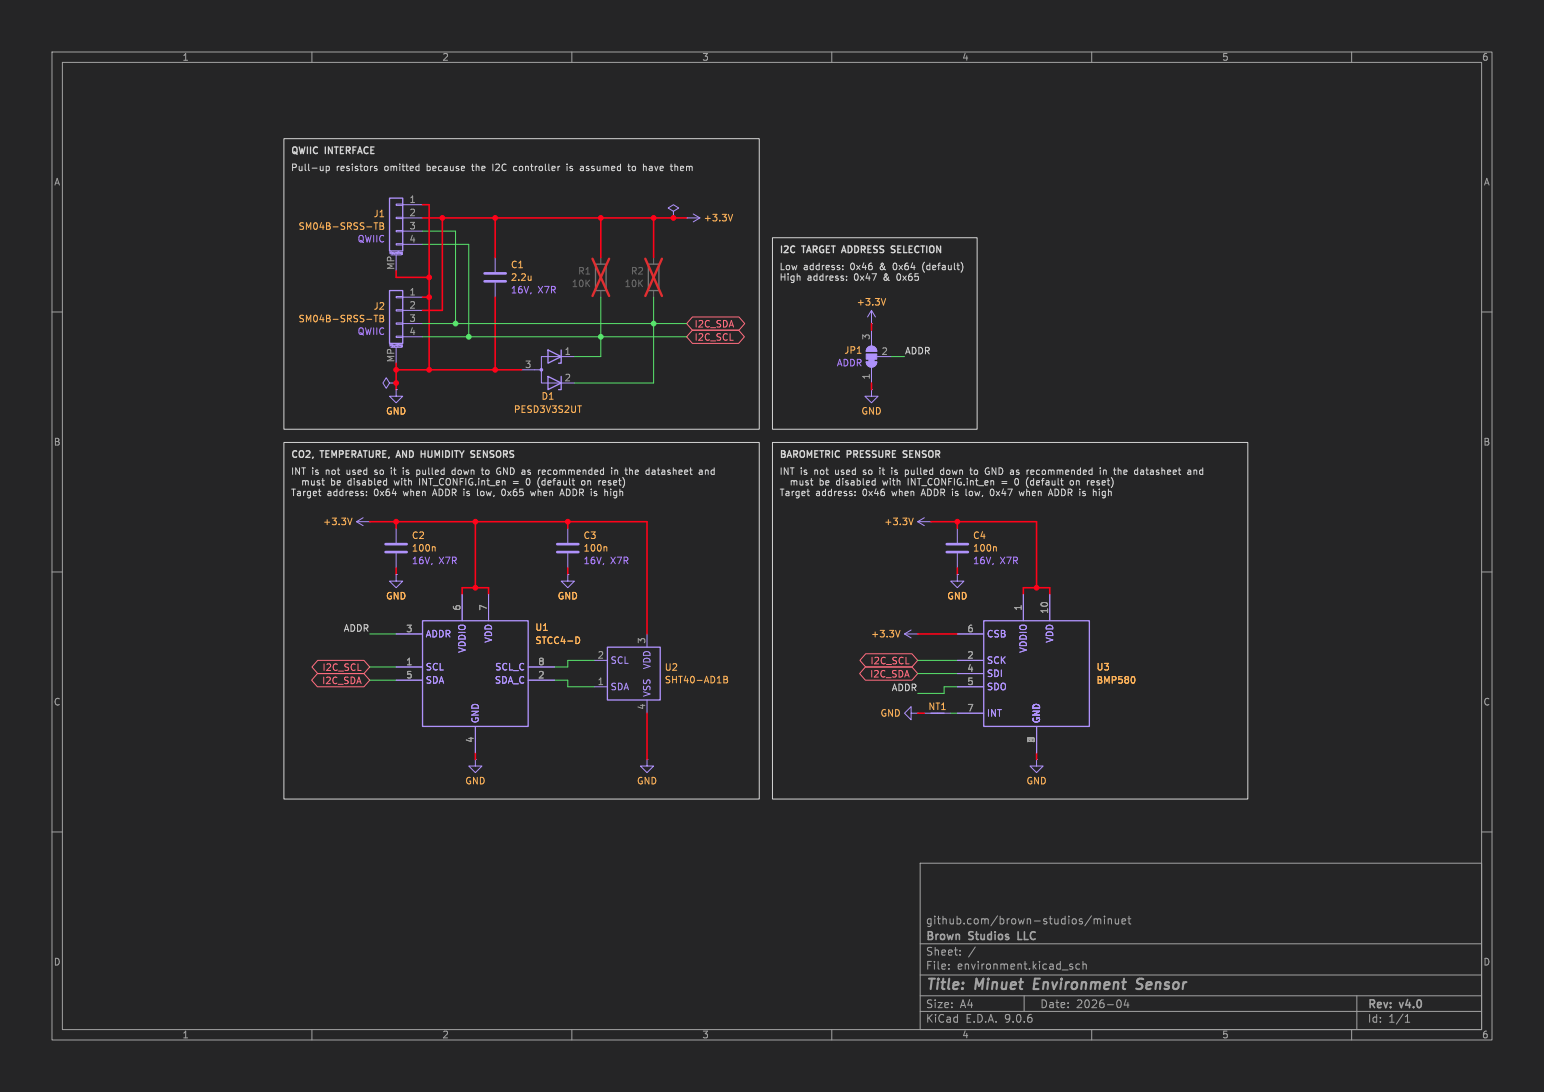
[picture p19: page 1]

BAROMETRIC PRESSURE SENSOR QWIIC INTERFACE

+3.3V GND
github.com/brown-studios/minuet GND

CO2, TEMPERATURE, AND HUMIDITY SENSORS

Target address: 0x64 when ADDR is low, 0x65 when ADDR is high

Target address: 0x46 when ADDR is low, 0x47 when ADDR is high GND

9 CSB 6 SCK 2 SDI 4 SDO 5 VDDIO

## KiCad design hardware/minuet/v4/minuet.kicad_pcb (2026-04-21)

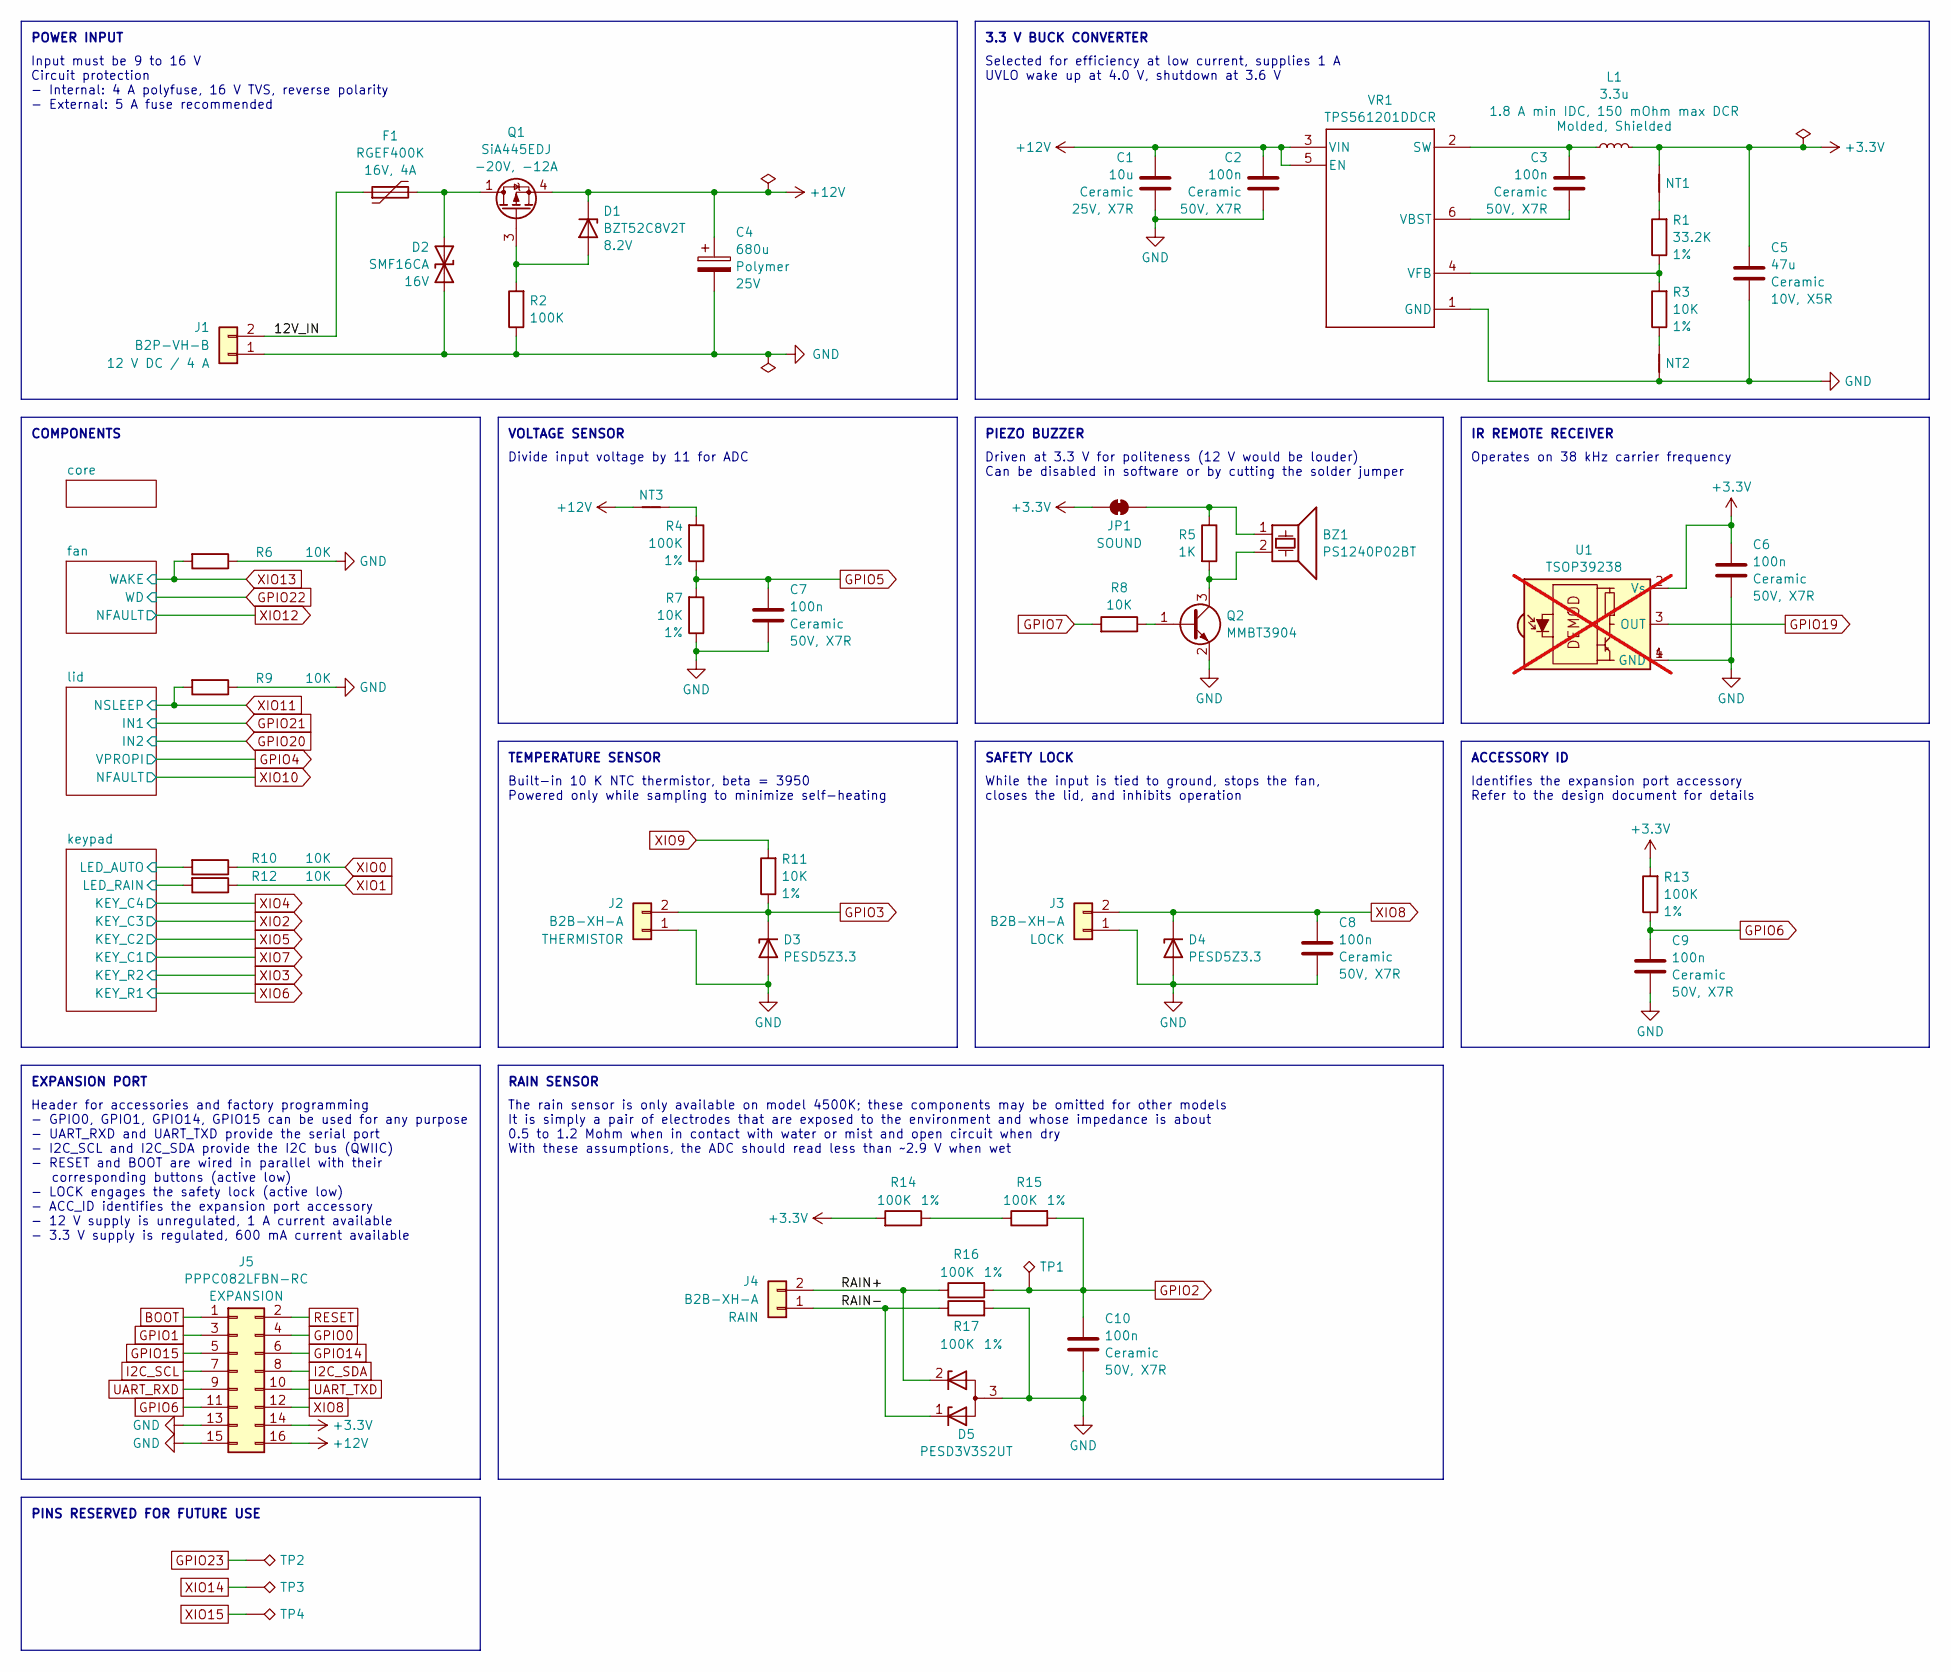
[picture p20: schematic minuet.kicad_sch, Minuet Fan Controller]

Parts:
BZ1: PS1240P02BT; Buzzer_TDK_PS1240P02BT_D12.2mm_H6.5mm; LCSC C76871
C1: 10u; C_1210_3225Metric; Rating 25V, X7R; Part CL32B106KAJNNNE; LCSC C39232
C2, C3, C6, C7, C8, C9, C10: 100n; C_0603_1608Metric; Rating 50V, X7R; LCSC C14663
C4: 680u; CP_Radial_D8.0mm_P3.50mm; Rating 25V; LCSC C5243855
C5: 47u; C_1206_3216Metric; Rating 10V, X5R; LCSC C96123
D1: BZT52C8V2T; D_SOD-523; Rating 8.2V; LCSC C5125761
D2: SMF16CA; D_SMF; Rating 16V; LCSC C1851354
D3, D4: PESD5Z3.3; D_SOD-523; LCSC C182940
D5: PESD3V3S2UT; SOT-23; LCSC C84276
F1: RGEF400K; Rating 16V, 4A; LCSC C135392
J1: B2P-VH-B; JST_VH_B2P-VH-B_1x02_P3.96mm_Vertical; LCSC C265114
J2, J3, J4: B2B-XH-A; JST_XH_B2B-XH-A_1x02_P2.50mm_Vertical; LCSC C158012
J5: PPPC082LFBN-RC; PinSocket_2x08_P2.54mm_Vertical; LCSC C30734
JP1: SolderJumper_2_Bridged; SolderJumper-2_P1.3mm_Bridged_RoundedPad1.0x1.5mm
L1: 3.3u; L_1008_2520Metric; Rating 1.8 A min IDC, 150 mOhm max DCR; Part AOTA-B252010S3R3MT; LCSC C22416628
NT1, NT2, NT3: NetTie_2; NetTie-2_SMD_Pad0.2mm
Q1: SiA445EDJ; Vishay_PowerPAK_SC70-6L_Single; Rating -20V, -12A; LCSC C144959
Q2: MMBT3904; SOT-23; LCSC C20526
R1: 33.2K; R_0603_1608Metric; Rating 1%; LCSC C4216
R2, R4, R13, R14, R15, R16, R17: 100K; R_0603_1608Metric; Rating 1%; LCSC C25803
R3, R6, R7, R8, R9, R10, R11, R12: 10K; R_0603_1608Metric; Rating 1%; LCSC C25804
R5: 1K; R_0603_1608Metric; Rating 1%; LCSC C21190
TP1, TP2, TP3, TP4: TestPoint_Alt; TestPoint_Pad_D1.0mm
U1: TSOP39238; TSOP39238_Standoff; LCSC C7128407; not fitted
VR1: TPS561201DDCR; SOT95P280X110-6N; LCSC C220433

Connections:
+3.3V: C5.1, C6.1, J5.14, JP1.1 (A), L1.1, NT1.2, R13.2, R14.2, U1.2 (Vs); also elsewhere on the board
+12V: C1.1, C2.1, C4.1, D1.1 (K), J5.16, NT3.1, Q1.4 (S), VR1.3 (VIN), VR1.5 (EN); also elsewhere on the board
/12V_IN: F1.1, J1.2
/RAIN+: D5.2 (K), J4.2, R16.1
/RAIN-: D5.1 (K), J4.1, R17.1
/keypad/LED_AUTO: R10.2; also elsewhere on the board
/keypad/LED_RAIN: R12.2; also elsewhere on the board
BOOT: J5.1; also elsewhere on the board
GND: C1.2, C2.2, C4.2, C5.2, C6.2, C7.2, C8.2, C9.2, C10.2, D2.1 (A1), D3.2 (A), D4.2 (A), D5.3 (A), J1.1, J2.1, J3.1, J5.13, J5.15, NT2.1, Q2.2 (E), R2.1, R6.1, R7.1, R9.1, R17.2, U1.1 (GND), U1.4 (GND), VR1.1 (GND); also elsewhere on the board
GPIO0: J5.4; also elsewhere on the board
GPIO1: J5.3; also elsewhere on the board
GPIO2: C10.1, R15.2, R16.2, TP1.1; also elsewhere on the board
GPIO3: D3.1 (K), J2.2, R11.1; also elsewhere on the board
GPIO5: C7.1, R4.1, R7.2; also elsewhere on the board
GPIO6: C9.1, J5.11, R13.1; also elsewhere on the board
GPIO7: R8.2; also elsewhere on the board
GPIO14: J5.6; also elsewhere on the board
GPIO15: J5.5; also elsewhere on the board
GPIO19: U1.3 (OUT); also elsewhere on the board
GPIO23: TP2.1; also elsewhere on the board
I2C_SCL: J5.7; also elsewhere on the board
I2C_SDA: J5.8; also elsewhere on the board
unnamed: D1.2 (A), Q1.3 (G), R2.2
unnamed: D2.2 (A2), F1.2, Q1.1 (D)
unnamed: BZ1.1, JP1.2 (B), R5.1
unnamed: NT1.1, R1.2
unnamed: NT2.2, R3.1
unnamed: NT3.2, R4.2
unnamed: Q2.1 (B), R8.1
unnamed: BZ1.2, Q2.3 (C), R5.2
unnamed: R14.1, R15.1
unnamed: C3.1, L1.2, VR1.2 (SW)
unnamed: C3.2, VR1.6 (VBST)
unnamed: R1.1, R3.2, VR1.4 (VFB)
RESET: J5.2; also elsewhere on the board
UART_RXD: J5.9; also elsewhere on the board
UART_TXD: J5.10; also elsewhere on the board
XIO0: R10.1; also elsewhere on the board
XIO1: R12.1; also elsewhere on the board
XIO8: C8.1, D4.1 (K), J3.2, J5.12; also elsewhere on the board
XIO9: R11.2; also elsewhere on the board
XIO11: R9.2; also elsewhere on the board
XIO13: R6.2; also elsewhere on the board
XIO14: TP3.1; also elsewhere on the board
XIO15: TP4.1; also elsewhere on the board

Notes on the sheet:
ACCESSORY ID
RAIN SENSOR
VOLTAGE SENSOR
Driven at 3.3 V for politeness (12 V would be louder) Can be disabled in software or by cutting the solder jumper
POWER INPUT
Identifies the expansion port accessory Refer to the design document for details
3.3 V BUCK CONVERTER
EXPANSION PORT
Operates on 38 kHz carrier frequency
The rain sensor is only available on model 4500K; these components may be omitted for other models It is simply a pair of electrodes that are exposed to the environment and whose impedance is about 0.5 to 1.2 Mohm when in contact with water or mist and open circuit when dry With these assumptions, 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
Input must be 9 to 16 V Circuit protection - Internal: 4 A polyfuse, 16 V TVS, reverse polarity - External: 5 A fuse recommended
Header for accessories and factory programming - GPIO0, GPIO1, GPIO14, GPIO15 can be used for any purpose - UART_RXD and UART_TXD provide the serial port - I2C_SCL and I2C_SDA provide the I2C bus (QWIIC) - RESET and BOOT are wired in parallel with their corresponding buttons (active low) - LOCK eng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
While the input is tied to ground, stops the fan, closes the lid, and inhibits operation
PINS RESERVED FOR FUTURE USE
IR REMOTE RECEIVER
PIEZO BUZZER
Selected for efficiency at low current, supplies 1 A UVLO wake up at 4.0 V, shutdown at 3.6 V
TEMPERATURE SENSOR
Divide input voltage by 11 for ADC
Built-in 10 K NTC thermistor, beta = 3950 Powered only while sampling to minimize self-heating
SAFETY LOCK
COMPONENTS

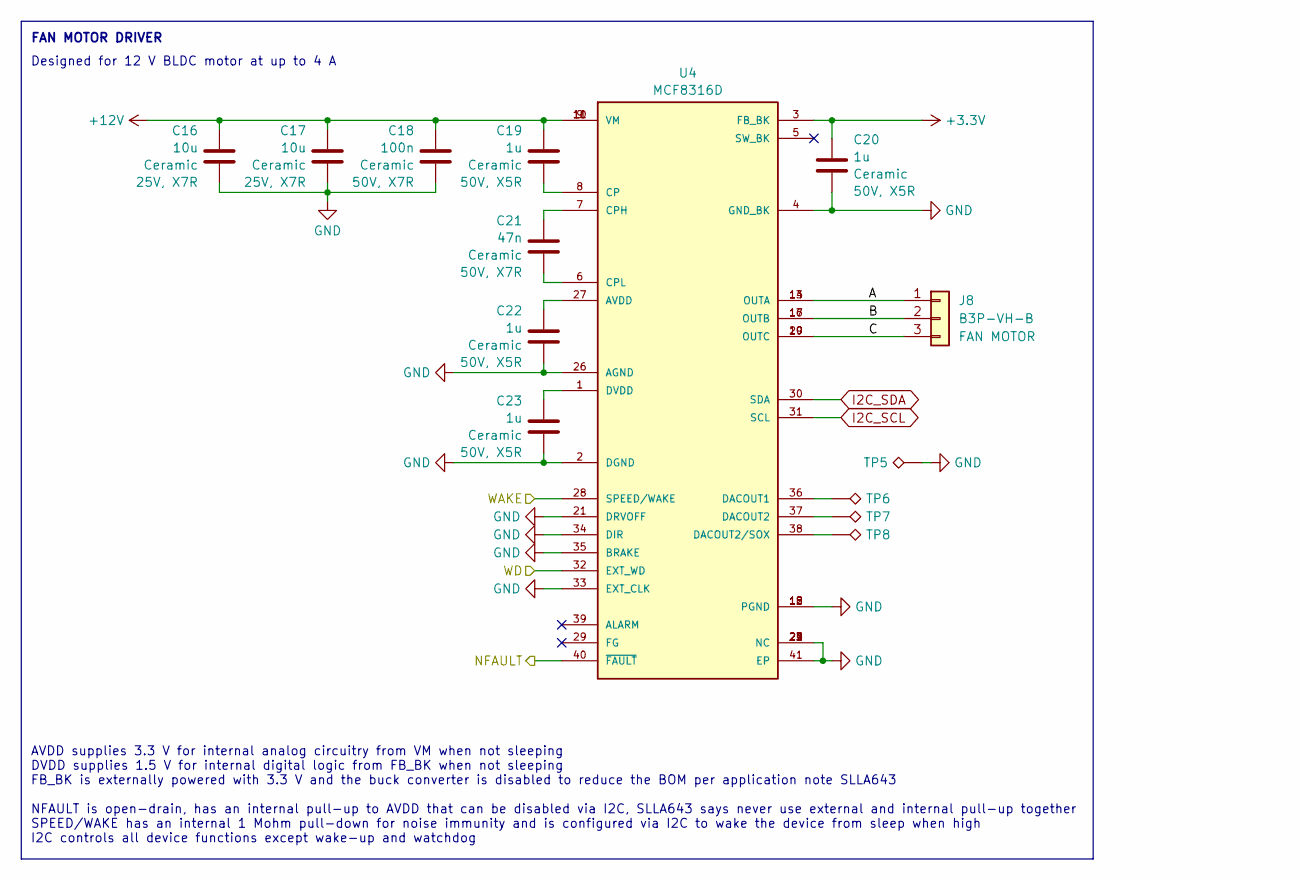
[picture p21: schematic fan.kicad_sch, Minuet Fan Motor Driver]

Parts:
C16, C17: 10u; C_1210_3225Metric; Rating 25V, X7R; Part CL32B106KAJNNNE; LCSC C39232
C18: 100n; C_0603_1608Metric; Rating 50V, X7R; LCSC C14663
C19, C20, C22, C23: 1u; C_0603_1608Metric; Rating 50V, X5R; LCSC C15849
C21: 47n; C_0603_1608Metric; Rating 50V, X7R; LCSC C1622
J8: B3P-VH-B; JST_VH_B3P-VH-B_1x03_P3.96mm_Vertical; LCSC C265360
TP5, TP6, TP7, TP8: TestPoint_Alt; TestPoint_Pad_D1.0mm
U4: MCF8316D; LCSC C42453588

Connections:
+3.3V: C20.1, U4.3 (FB_BK); also elsewhere on the board
+12V: C16.1, C17.1, C18.1, C19.1, U4.9 (VM), U4.10 (VM), U4.11 (VM); also elsewhere on the board
/fan/A: J8.1, U4.13 (OUTA), U4.14 (OUTA)
/fan/B: J8.2, U4.16 (OUTB), U4.17 (OUTB)
/fan/C: J8.3, U4.19 (OUTC), U4.20 (OUTC)
GND: C16.2, C17.2, C18.2, C20.2, C22.2, C23.2, TP5.1, U4.2 (DGND), U4.4 (GND_BK), U4.12 (PGND), U4.15 (PGND), U4.18 (PGND), U4.21 (DRVOFF), U4.22 (NC), U4.23 (NC), U4.24 (NC), U4.25 (NC), U4.26 (AGND), U4.33 (EXT_CLK), U4.34 (DIR), U4.35 (BRAKE), U4.41 (EP); also elsewhere on the board
GPIO22: U4.32 (EXT_WD); also elsewhere on the board
I2C_SCL: U4.31 (SCL); also elsewhere on the board
I2C_SDA: U4.30 (SDA); also elsewhere on the board
unnamed: C22.1, U4.27 (AVDD)
unnamed: C19.2, U4.8 (CP)
unnamed: C21.1, U4.7 (CPH)
unnamed: C21.2, U4.6 (CPL)
unnamed: TP6.1, U4.36 (DACOUT1)
unnamed: TP7.1, U4.37 (DACOUT2)
unnamed: TP8.1, U4.38 (DACOUT2/SOX)
unnamed: C23.1, U4.1 (DVDD)
XIO12: U4.40 (~FAULT); also elsewhere on the board
XIO13: U4.28 (SPEED/WAKE); also elsewhere on the board

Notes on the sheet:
FAN MOTOR DRIVER
Designed for 12 V BLDC motor at up to 4 A
AVDD supplies 3.3 V for internal analog circuitry from VM when not sleeping DVDD supplies 1.5 V for internal digital logic from FB_BK when not sleeping FB_BK is externally powered with 3.3 V and the buck converter is disabled to reduce the BOM per application note SLLA643 NFAULT is open-drain, has 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

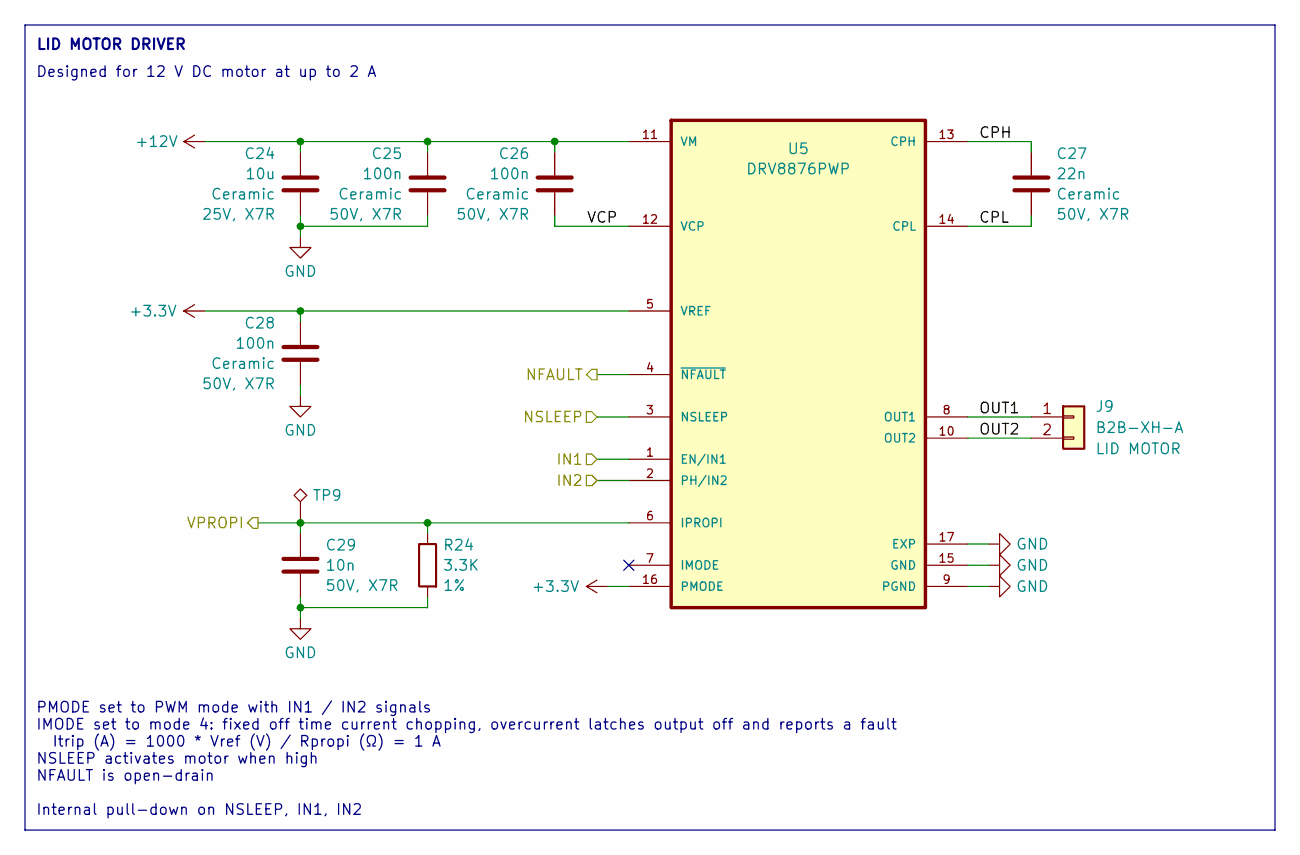
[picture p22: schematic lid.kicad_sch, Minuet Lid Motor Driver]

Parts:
C24: 10u; C_1210_3225Metric; Rating 25V, X7R; Part CL32B106KAJNNNE; LCSC C39232
C25, C26, C28: 100n; C_0603_1608Metric; Rating 50V, X7R; LCSC C14663
C27: 22n; C_0603_1608Metric; Rating 50V, X7R; LCSC C21122
C29: 10n; C_0603_1608Metric; Rating 50V, X7R; LCSC C57112
J9: B2B-XH-A; JST_XH_B2B-XH-A_1x02_P2.50mm_Vertical; LCSC C158012
R24: 3.3K; R_0603_1608Metric; Rating 1%; LCSC C22978
TP9: TestPoint_Alt; TestPoint_Pad_D1.0mm
U5: DRV8876PWP; IC_DRV8876PWPR; PARTREV E; LCSC C575551

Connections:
+3.3V: C28.1, U5.5 (VREF), U5.16 (PMODE); also elsewhere on the board
+12V: C24.1, C25.1, C26.1, U5.11 (VM); also elsewhere on the board
/lid/CPH: C27.1, U5.13 (CPH)
/lid/CPL: C27.2, U5.14 (CPL)
/lid/OUT1: J9.1, U5.8 (OUT1)
/lid/OUT2: J9.2, U5.10 (OUT2)
/lid/VCP: C26.2, U5.12 (VCP)
GND: C24.2, C25.2, C28.2, C29.2, R24.2, U5.9 (PGND), U5.15 (GND), U5.17 (EXP); also elsewhere on the board
GPIO4: C29.1, R24.1, TP9.1, U5.6 (IPROPI); also elsewhere on the board
GPIO20: U5.2 (PH/IN2); also elsewhere on the board
GPIO21: U5.1 (EN/IN1); also elsewhere on the board
XIO10: U5.4 (~NFAULT); also elsewhere on the board
XIO11: U5.3 (NSLEEP); also elsewhere on the board

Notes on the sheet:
PMODE set to PWM mode with IN1 / IN2 signals IMODE set to mode 4: fixed off time current chopping, overcurrent latches output off and reports a fault Itrip (A) = 1000 * Vref (V) / Rpropi (Ω) = 1 A NSLEEP activates motor when high NFAULT is open-drain Internal pull-down on NSLEEP, IN1, IN2
Designed for 12 V DC motor at up to 2 A
LID MOTOR DRIVER

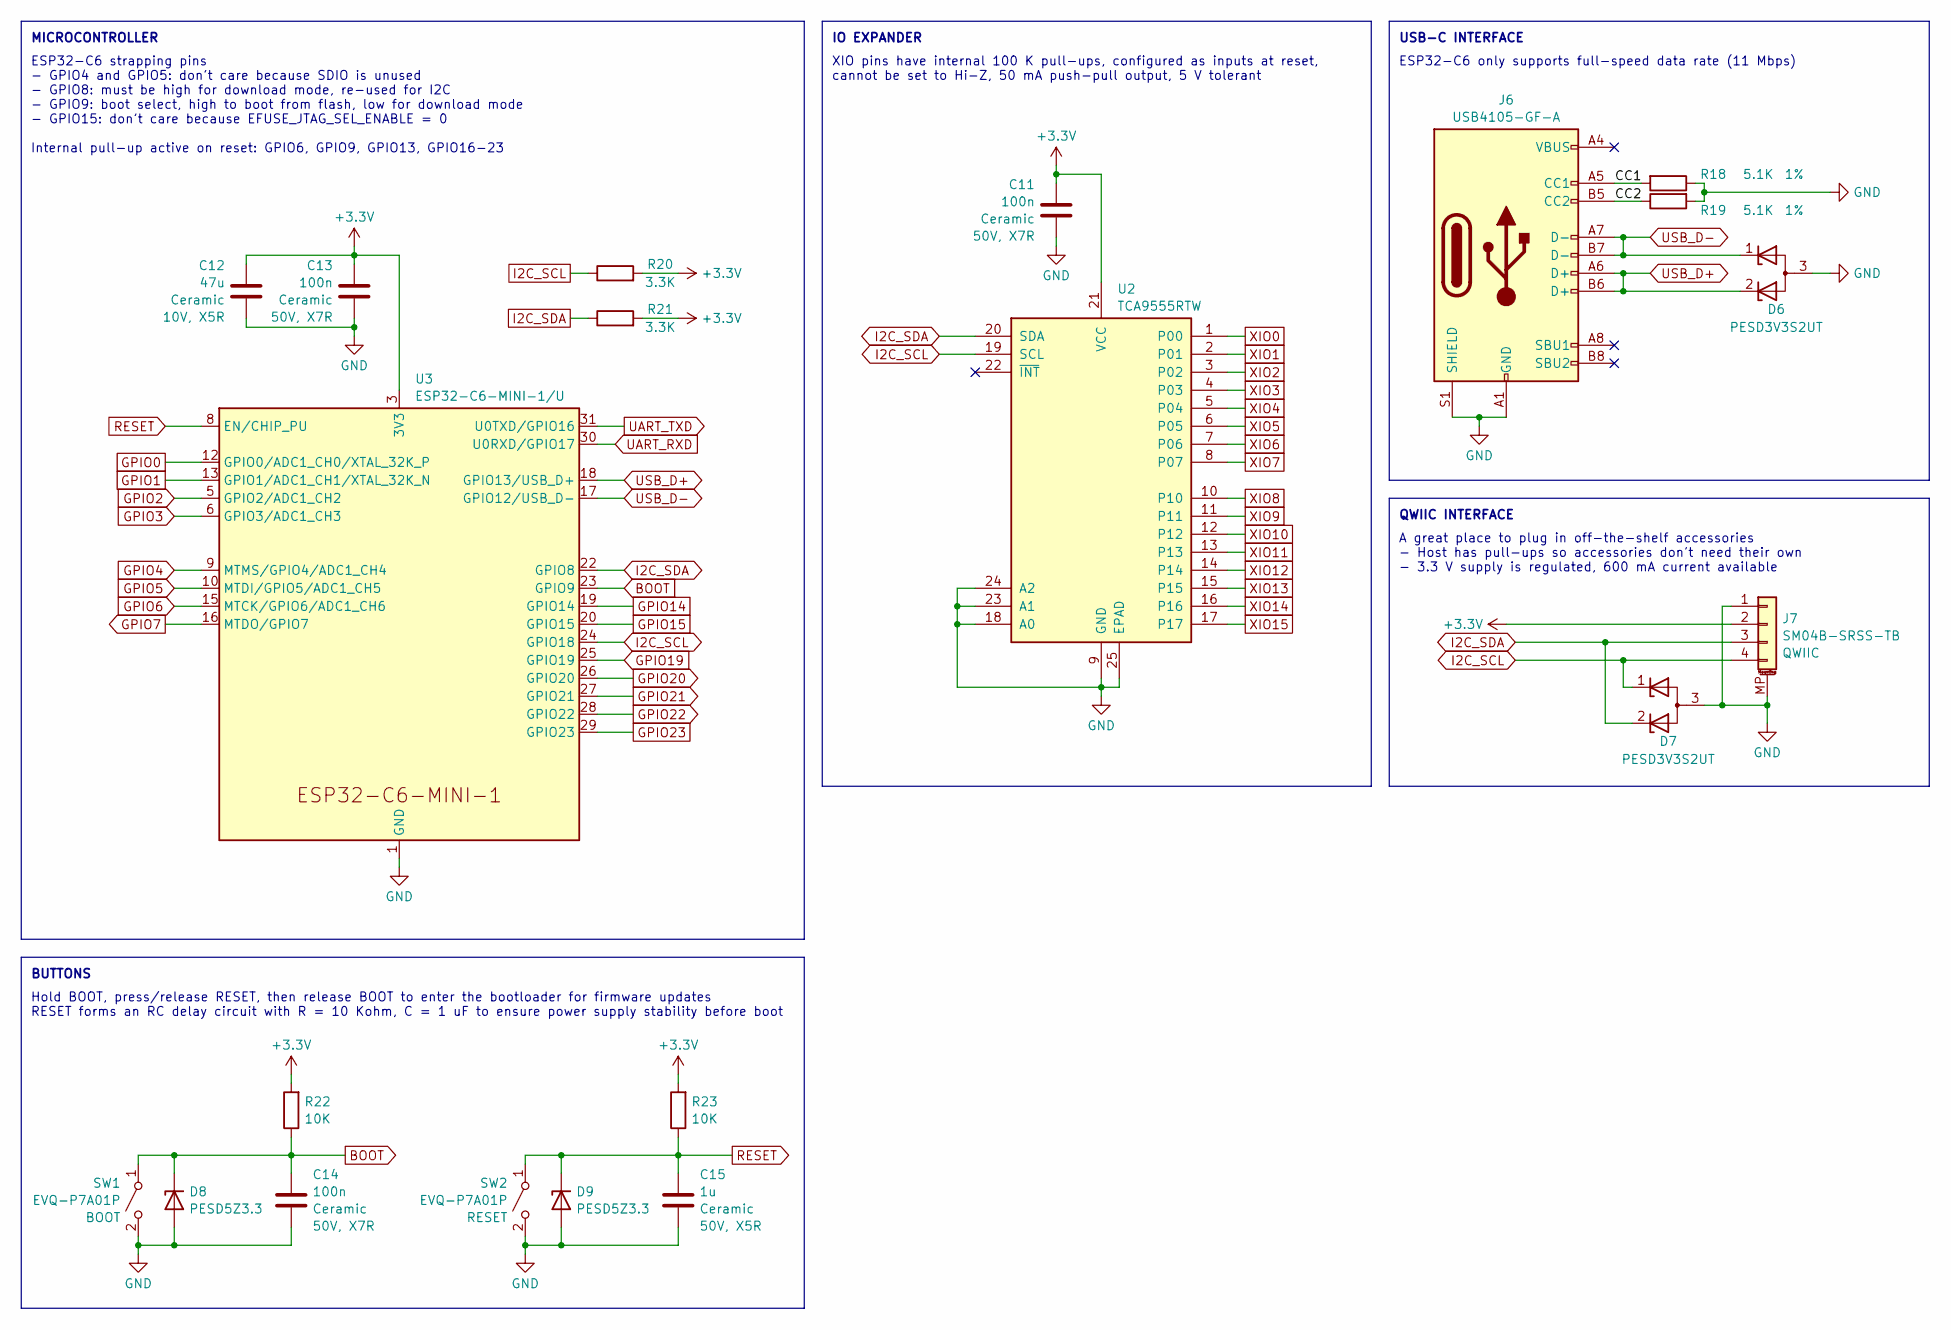
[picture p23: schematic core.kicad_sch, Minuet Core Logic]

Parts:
C11, C13, C14: 100n; C_0603_1608Metric; Rating 50V, X7R; LCSC C14663
C12: 47u; C_1206_3216Metric; Rating 10V, X5R; LCSC C96123
C15: 1u; C_0603_1608Metric; Rating 50V, X5R; LCSC C15849
D6, D7: PESD3V3S2UT; SOT-23; LCSC C84276
D8, D9: PESD5Z3.3; D_SOD-523; LCSC C182940
J6: USB4105-GF-A; USB_C_Receptacle_GCT_USB4105-xx-A_16P_TopMnt_Horizontal; LCSC C2988369
J7: SM04B-SRSS-TB; JST_SH_SM04B-SRSS-TB_1x04-1MP_P1.00mm_Horizontal; LCSC C160404
R18, R19: 5.1K; R_0603_1608Metric; Rating 1%; LCSC C23186
R20, R21: 3.3K; R_0603_1608Metric; Rating 1%; LCSC C22978
R22, R23: 10K; R_0603_1608Metric; Rating 1%; LCSC C25804
SW1, SW2: EVQ-P7A01P; SW_SPST_EVQP7A; LCSC C79167
U2: TCA9555RTW; WQFN-24-1EP_4x4mm_P0.5mm_EP2.45x2.45mm; LCSC C140277
U3: ESP32-C6-MINI-1/U; ESP32-C6-MINI-1; LCSC C5736265

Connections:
+3.3V: C11.1, C12.1, C13.1, J7.2, R20.2, R21.2, R22.2, R23.2, U2.21 (VCC), U3.3 (3V3); also elsewhere on the board
/core/CC1: J6.A5 (CC1), R18.2
/core/CC2: J6.B5 (CC2), R19.1
BOOT: C14.1, D8.1 (K), R22.1, SW1.1 (A), U3.23 (GPIO9); also elsewhere on the board
GND: C11.2, C12.2, C13.2, C14.2, C15.2, D6.3 (A), D7.3 (A), D8.2 (A), D9.2 (A), J6.A1 (GND), J6.A12 (GND), J6.B1 (GND), J6.B12 (GND), J6.S1 (SHIELD), J7.1, J7.MP (MountPin), R18.1, R19.2, SW1.2 (B), SW2.2 (B), U2.9 (GND), U2.18 (A0), U2.23 (A1), U2.24 (A2), U2.25 (EPAD), U3.1 (GND), U3.2 (GND), U3.11 (GND), U3.14 (GND), U3.36 (GND), U3.37 (GND), U3.38 (GND), U3.39 (GND), U3.40 (GND), U3.41 (GND), U3.42 (GND), U3.43 (GND), U3.44 (GND), U3.45 (GND), U3.46 (GND), U3.47 (GND), U3.48 (GND), U3.49 (GND), U3.50 (GND), U3.51 (GND), U3.52 (GND), U3.53 (GND); also elsewhere on the board
GPIO0: U3.12 (GPIO0/ADC1_CH0/XTAL_32K_P); also elsewhere on the board
GPIO1: U3.13 (GPIO1/ADC1_CH1/XTAL_32K_N); also elsewhere on the board
GPIO2: U3.5 (GPIO2/ADC1_CH2); also elsewhere on the board
GPIO3: U3.6 (GPIO3/ADC1_CH3); also elsewhere on the board
GPIO4: U3.9 (MTMS/GPIO4/ADC1_CH4); also elsewhere on the board
GPIO5: U3.10 (MTDI/GPIO5/ADC1_CH5); also elsewhere on the board
GPIO6: U3.15 (MTCK/GPIO6/ADC1_CH6); also elsewhere on the board
GPIO7: U3.16 (MTDO/GPIO7); also elsewhere on the board
GPIO14: U3.19 (GPIO14); also elsewhere on the board
GPIO15: U3.20 (GPIO15); also elsewhere on the board
GPIO19: U3.25 (GPIO19); also elsewhere on the board
GPIO20: U3.26 (GPIO20); also elsewhere on the board
GPIO21: U3.27 (GPIO21); also elsewhere on the board
GPIO22: U3.28 (GPIO22); also elsewhere on the board
GPIO23: U3.29 (GPIO23); also elsewhere on the board
I2C_SCL: D7.1 (K), J7.4, R20.1, U2.19 (SCL), U3.24 (GPIO18); also elsewhere on the board
I2C_SDA: D7.2 (K), J7.3, R21.1, U2.20 (SDA), U3.22 (GPIO8); also elsewhere on the board
RESET: C15.1, D9.1 (K), R23.1, SW2.1 (A), U3.8 (EN/CHIP_PU); also elsewhere on the board
UART_RXD: U3.30 (U0RXD/GPIO17); also elsewhere on the board
UART_TXD: U3.31 (U0TXD/GPIO16); also elsewhere on the board
USB_D+: D6.2 (K), J6.A6 (D+), J6.B6 (D+), U3.18 (GPIO13/USB_D+)
USB_D-: D6.1 (K), J6.A7 (D-), J6.B7 (D-), U3.17 (GPIO12/USB_D-)
XIO0: U2.1 (P00); also elsewhere on the board
XIO1: U2.2 (P01); also elsewhere on the board
XIO2: U2.3 (P02); also elsewhere on the board
XIO3: U2.4 (P03); also elsewhere on the board
XIO4: U2.5 (P04); also elsewhere on the board
XIO5: U2.6 (P05); also elsewhere on the board
XIO6: U2.7 (P06); also elsewhere on the board
XIO7: U2.8 (P07); also elsewhere on the board
XIO8: U2.10; also elsewhere on the board
XIO9: U2.11; also elsewhere on the board
XIO10: U2.12; also elsewhere on the board
XIO11: U2.13; also elsewhere on the board
XIO12: U2.14; also elsewhere on the board
XIO13: U2.15; also elsewhere on the board
XIO14: U2.16; also elsewhere on the board
XIO15: U2.17; also elsewhere on the board

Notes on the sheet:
IO EXPANDER
USB-C INTERFACE
XIO pins have internal 100 K pull-ups, configured as inputs at reset, cannot be set to Hi-Z, 50 mA push-pull output, 5 V tolerant
ESP32-C6 strapping pins - GPIO4 and GPIO5: don't care because SDIO is unused - GPIO8: must be high for download mode, re-used for I2C - GPIO9: boot select, high to boot from flash, low for download mode - GPIO15: don't care because EFUSE_JTAG_SEL_ENABLE = 0 Internal pull-up active on reset: GPIO6, 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
Hold BOOT, press/release RESET, then release BOOT to enter the bootloader for firmware updates RESET forms an RC delay circuit with R = 10 Kohm, C = 1 uF to ensure power supply stability before boot
BUTTONS
ESP32-C6 only supports full-speed data rate (11 Mbps)
QWIIC INTERFACE
A great place to plug in off-the-shelf accessories - Host has pull-ups so accessories don't need their own - 3.3 V supply is regulated, 600 mA current available
MICROCONTROLLER

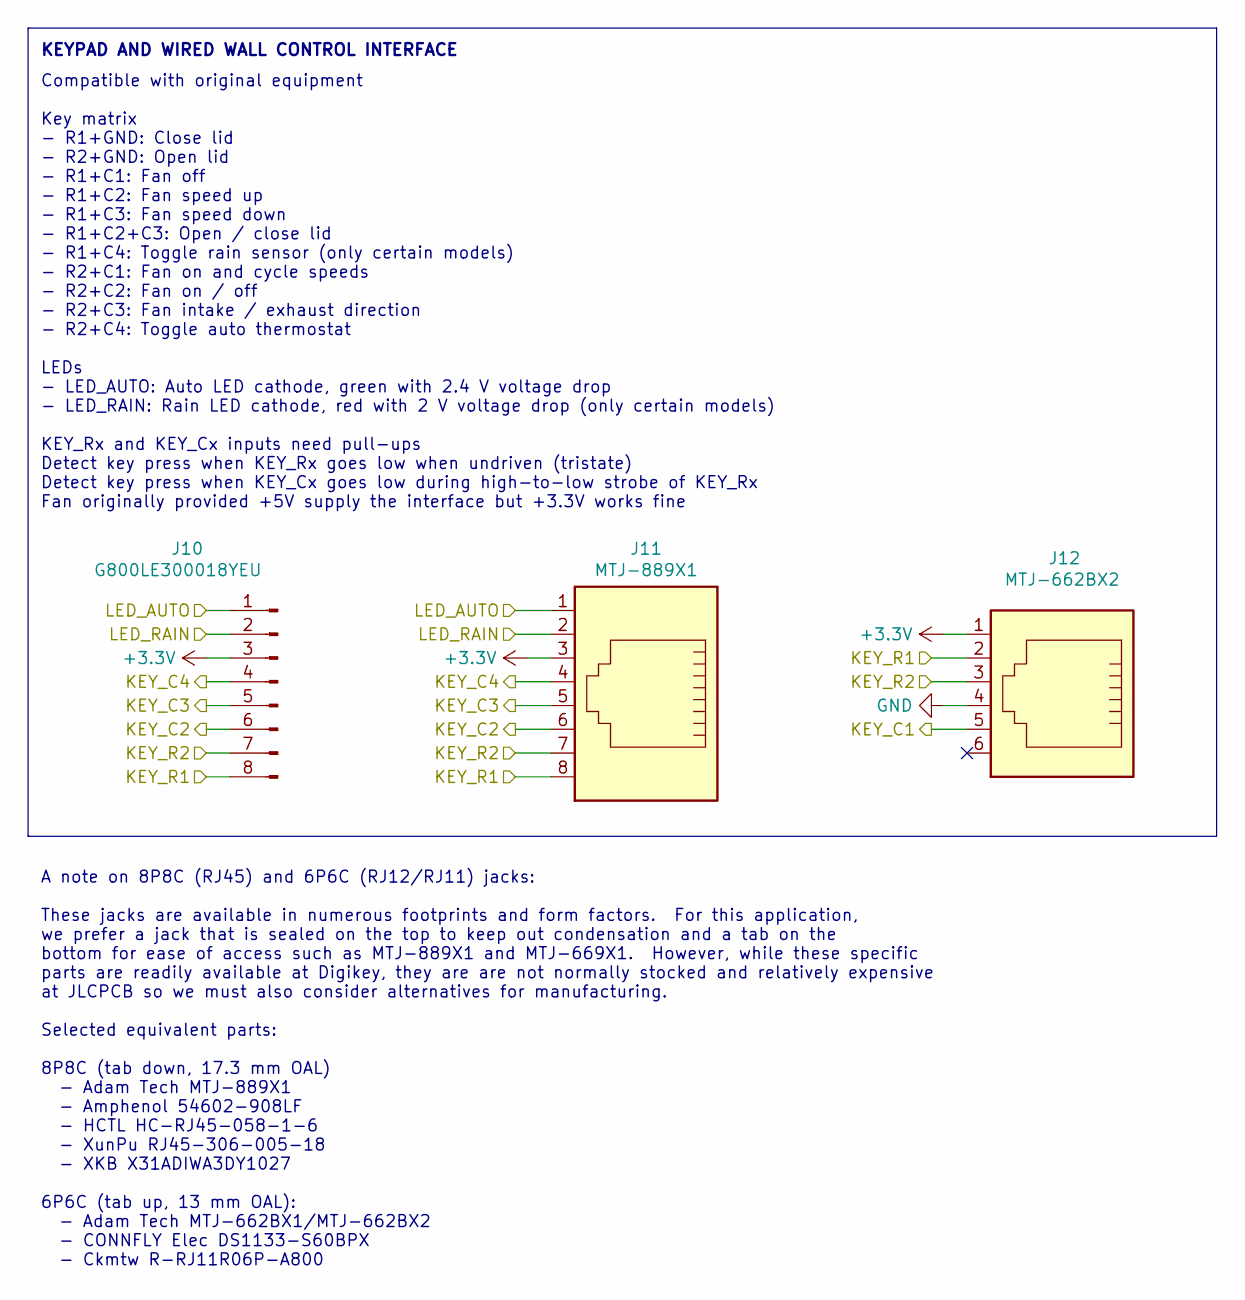
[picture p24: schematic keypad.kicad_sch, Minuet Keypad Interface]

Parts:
J10: G800LE300018YEU; PinHeader_1x08_P2.54mm_Vertical; LCSC_Preferred C3345591
J11: MTJ-889X1; LCSC C3000197
J12: MTJ-662BX2; LCSC C77859

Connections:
+3.3V: J10.3, J11.3, J12.1; also elsewhere on the board
/keypad/LED_AUTO: J10.1, J11.1; also elsewhere on the board
/keypad/LED_RAIN: J10.2, J11.2; also elsewhere on the board
GND: J12.4; also elsewhere on the board
XIO2: J10.5, J11.5; also elsewhere on the board
XIO3: J10.7, J11.7, J12.3; also elsewhere on the board
XIO4: J10.4, J11.4; also elsewhere on the board
XIO5: J10.6, J11.6; also elsewhere on the board
XIO6: J10.8, J11.8, J12.2; also elsewhere on the board
XIO7: J12.5; also elsewhere on the board

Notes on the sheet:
A note on 8P8C (RJ45) and 6P6C (RJ12/RJ11) jacks: These jacks are available in numerous footprints and form factors. For this application, we prefer a jack that is sealed on the top to keep out condensation and a tab on the bottom for ease of access such as MTJ-889X1 and MTJ-669X1. However, while t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
Compatible with original equipment Key matrix - R1+GND: Close lid - R2+GND: Open lid - R1+C1: Fan off - R1+C2: Fan speed up - R1+C3: Fan speed down - R1+C2+C3: Open / close lid - R1+C4: Toggle rain sensor (only certain models) - R2+C1: Fan on and cycle speeds - R2+C2: Fan on / off - R2+C3: Fan inta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
KEYPAD AND WIRED WALL CONTROL INTERFACE

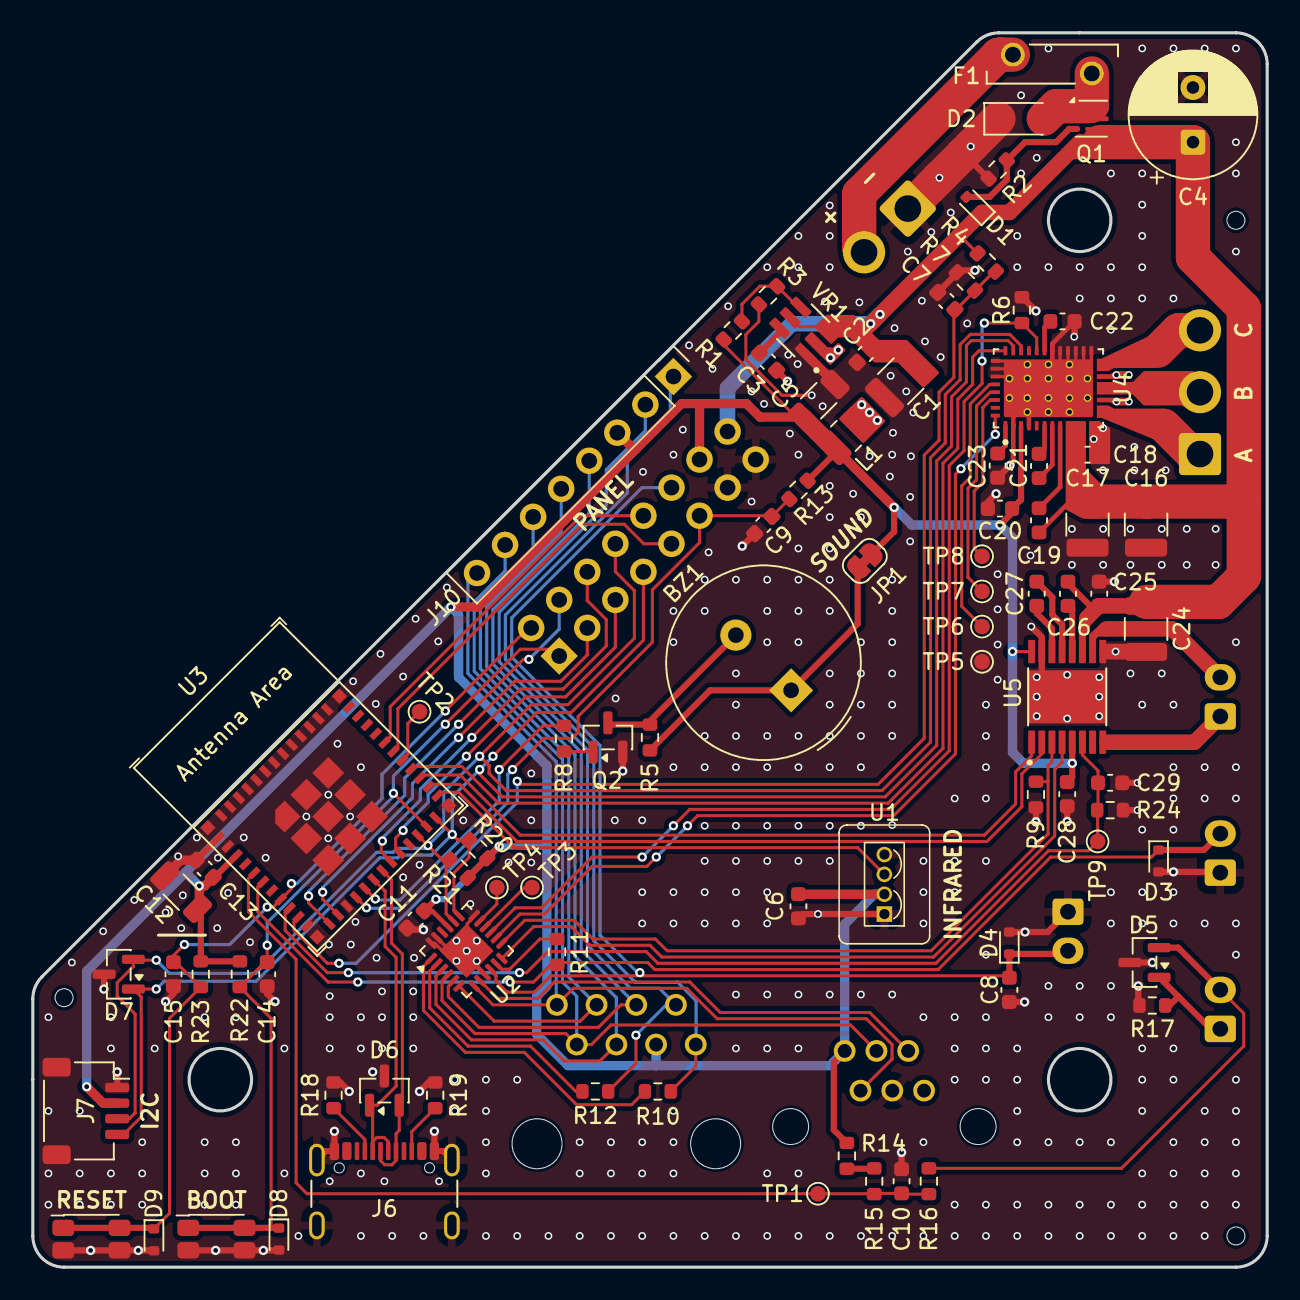
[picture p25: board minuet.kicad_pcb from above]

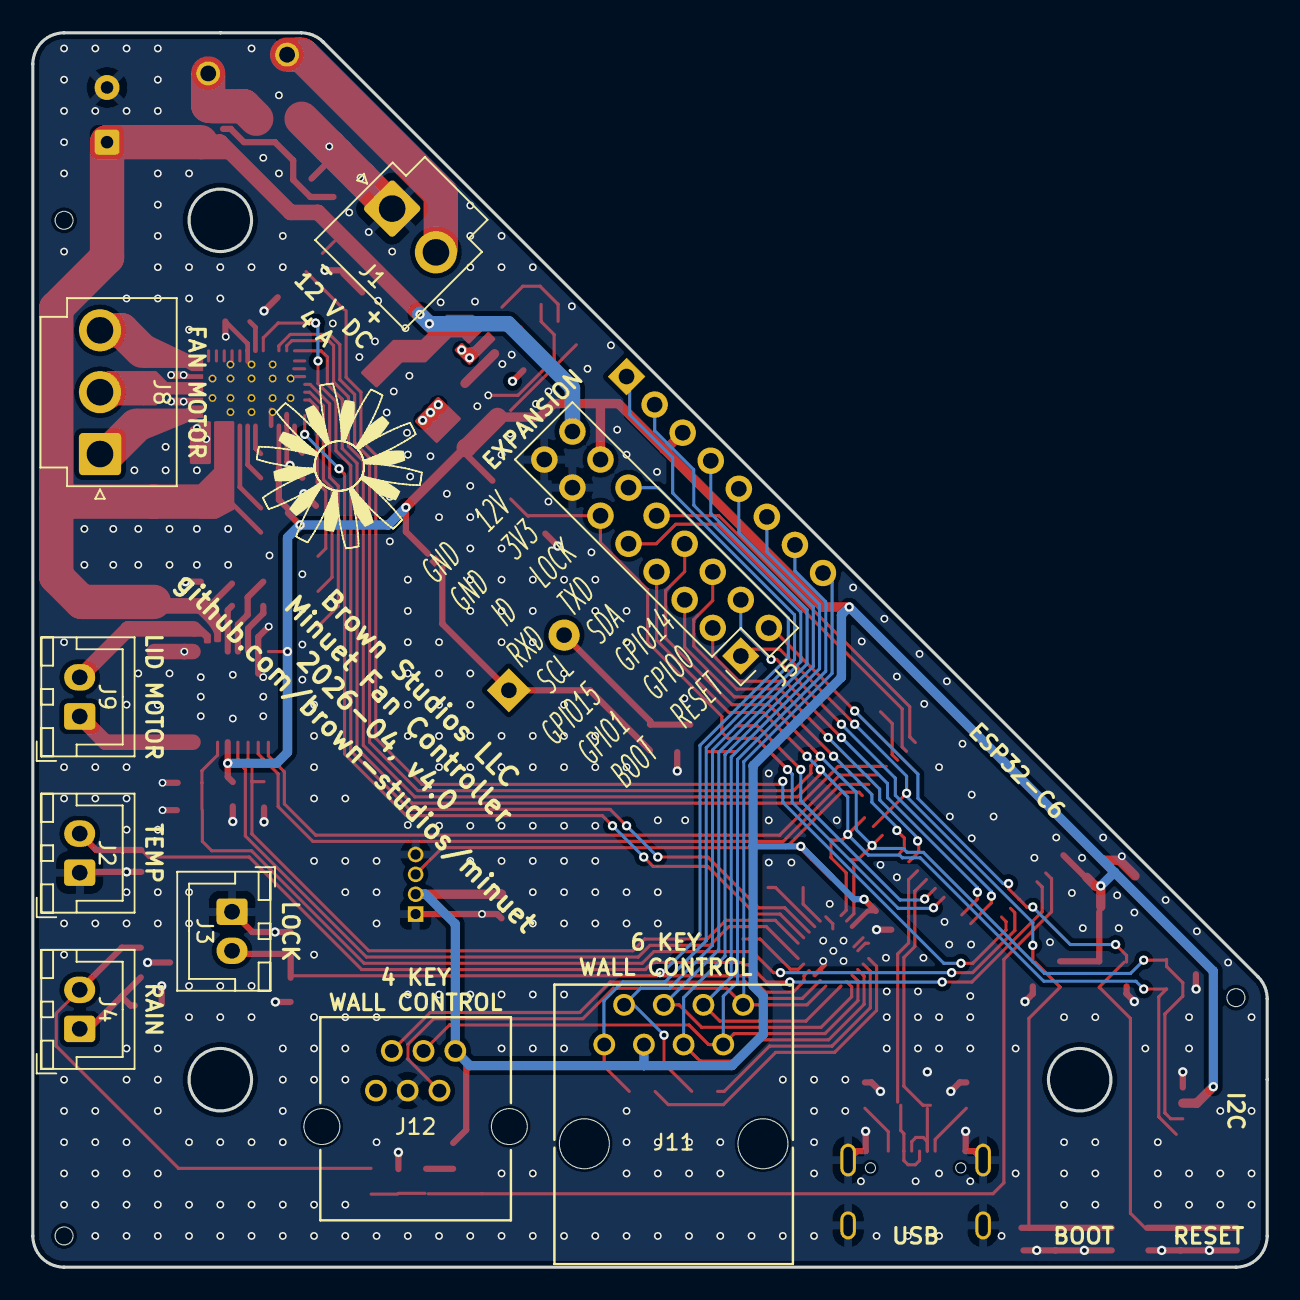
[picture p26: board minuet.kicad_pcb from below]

Board: 4 copper layers, 79.0 x 79.0 mm, 103 parts (9 on the bottom side), 77 nets.

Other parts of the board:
TH1, TH2, TH3: JLCPCB_PCBA_Tooling_Hole

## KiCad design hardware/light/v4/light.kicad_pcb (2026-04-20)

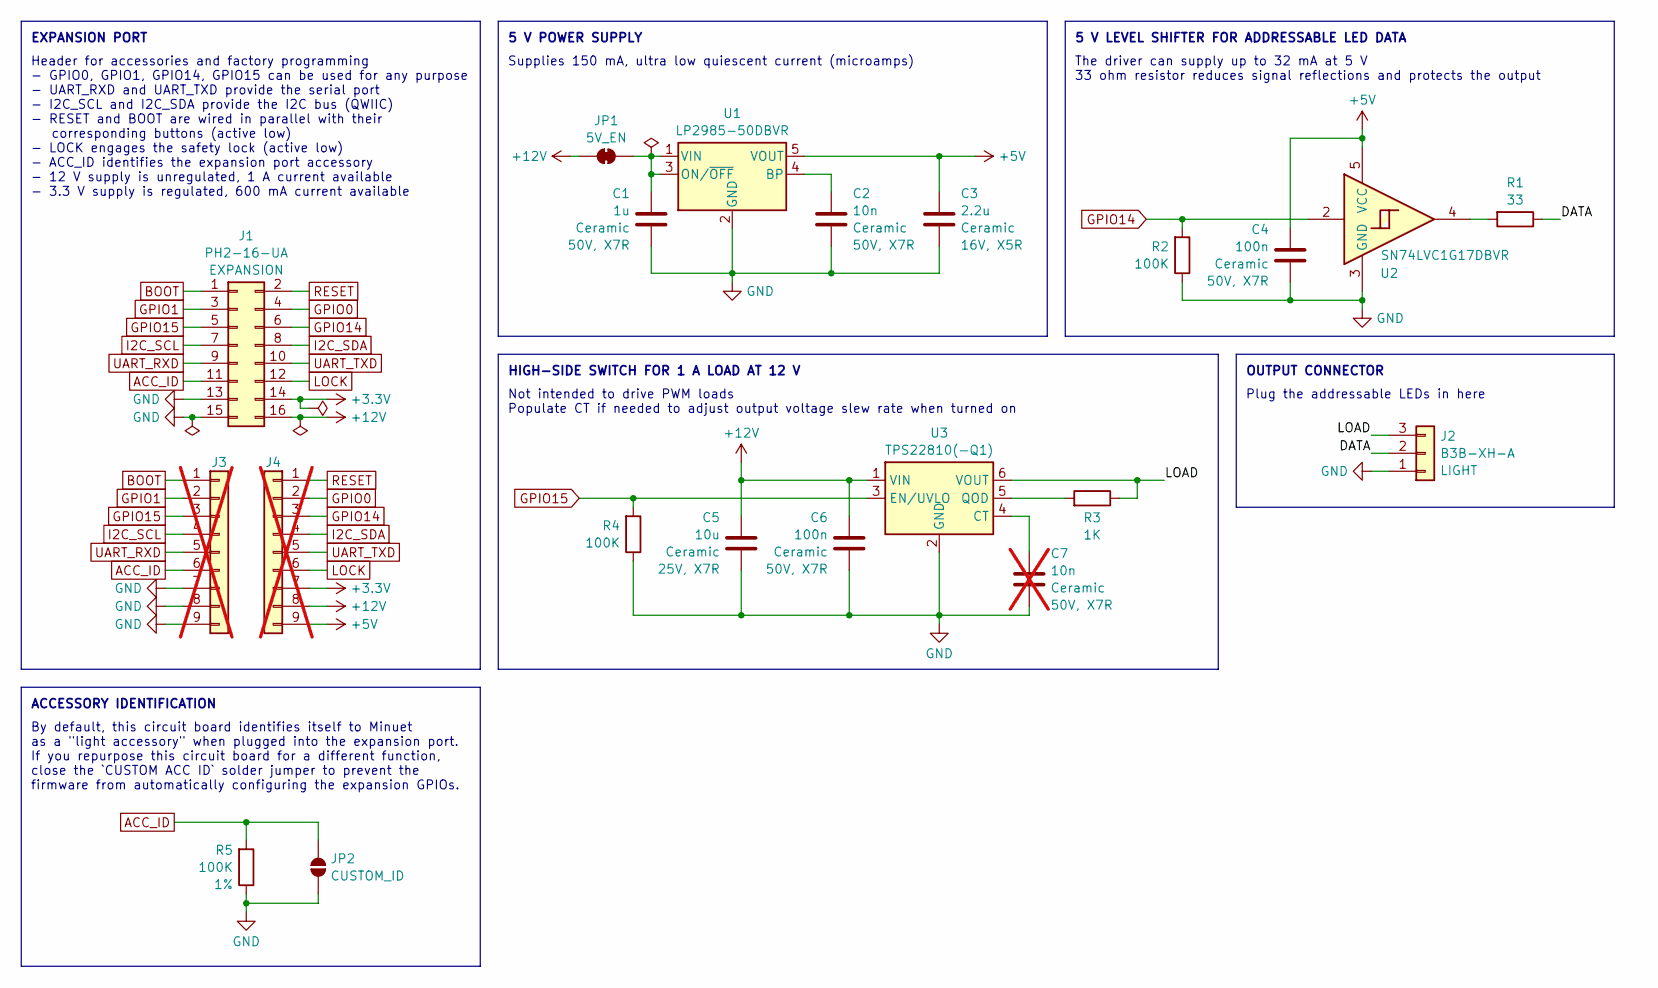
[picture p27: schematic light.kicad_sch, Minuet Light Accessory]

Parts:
C1: 1u; C_0805_2012Metric; Rating 50V, X7R; LCSC C28323
C2: 10n; C_0603_1608Metric; Rating 50V, X7R; LCSC C57112
C3: 2.2u; C_0603_1608Metric; Rating 16V, X5R; LCSC C23630
C4, C6: 100n; C_0603_1608Metric; Rating 50V, X7R; LCSC C14663
C5: 10u; C_1210_3225Metric; Rating 25V, X7R; Part CL32B106KAJNNNE; LCSC C39232
C7: 10n; C_0603_1608Metric; Rating 50V, X7R; LCSC C57112; not fitted
J1: PH2-16-UA; PinHeader_2x08_P2.54mm_Vertical; LCSC C492425
J2: B3B-XH-A; JST_XH_B3B-XH-A_1x03_P2.50mm_Vertical; LCSC C144394
J3, J4: Conn_01x09; Pins_1x09; not fitted
JP1: SolderJumper_2_Open; SolderJumper-2_P1.3mm_Bridged_RoundedPad1.0x1.5mm
JP2: SolderJumper_2_Open; SolderJumper-2_P1.3mm_Open_RoundedPad1.0x1.5mm
R1: 33; R_0603_1608Metric; Rating 1%; LCSC C23140
R2, R4, R5: 100K; R_0603_1608Metric; Rating 1%; LCSC C25803
R3: 1K; R_0603_1608Metric; Rating 1%; LCSC C21190
U1: LP2985-50DBVR; SOT-23-5; LCSC C74511
U2: SN74LVC1G17DBVR; SOT-23-5; LCSC C7836
U3: TPS22810(-Q1); SOT-23-6; LCSC C2877634

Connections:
+3.3V: J1.14, J4.7
+5V: C3.2, C4.1, J4.9, U1.5 (VOUT), U2.5 (VCC)
+12V: C5.1, C6.1, J1.16, J4.8, JP1.2 (B), U3.1 (VIN)
/DATA: J2.2, R1.1
/LOAD: J2.3, R3.1, U3.6 (VOUT)
ACC_ID: J1.11, J3.6, JP2.1 (A), R5.2
BOOT: J1.1, J3.1
GND: C1.2, C2.1, C3.1, C4.2, C5.2, C6.2, C7.1, J1.13, J1.15, J2.1, J3.7, J3.8, J3.9, JP2.2 (B), R2.1, R4.1, R5.1, U1.2 (GND), U2.3 (GND), U3.2 (GND)
GPIO0: J1.4, J4.2
GPIO1: J1.3, J3.2
GPIO14: J1.6, J4.3, R2.2, U2.2
GPIO15: J1.5, J3.3, R4.2, U3.3 (EN/UVLO)
I2C_SCL: J1.7, J3.4
I2C_SDA: J1.8, J4.4
LOCK: J1.12, J4.6
unnamed: C1.1, JP1.1 (A), U1.1 (VIN), U1.3 (ON/~OFF)
unnamed: R1.2, U2.4
unnamed: C2.2, U1.4 (BP)
unnamed: C7.2, U3.4 (CT)
unnamed: R3.2, U3.5 (QOD)
RESET: J1.2, J4.1
UART_RXD: J1.9, J3.5
UART_TXD: J1.10, J4.5

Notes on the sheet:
HIGH-SIDE SWITCH FOR 1 A LOAD AT 12 V
Not intended to drive PWM loads Populate CT if needed to adjust output voltage slew rate when turned on
Plug the addressable LEDs in here
The driver can supply up to 32 mA at 5 V 33 ohm resistor reduces signal reflections and protects the output
By default, this circuit board identifies itself to Minuet as a "light accessory" when plugged into the expansion port. If you repurpose this circuit board for a different function, close the `CUSTOM ACC ID` solder jumper to prevent the firmware from automatically configuring the expansion GPIOs.
ACCESSORY IDENTIFICATION
Header for accessories and factory programming - GPIO0, GPIO1, GPIO14, GPIO15 can be used for any purpose - UART_RXD and UART_TXD provide the serial port - I2C_SCL and I2C_SDA provide the I2C bus (QWIIC) - RESET and BOOT are wired in parallel with their corresponding buttons (active low) - LOCK eng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
5 V LEVEL SHIFTER FOR ADDRESSABLE LED DATA
EXPANSION PORT
Supplies 150 mA, ultra low quiescent current (microamps)
5 V POWER SUPPLY
OUTPUT CONNECTOR

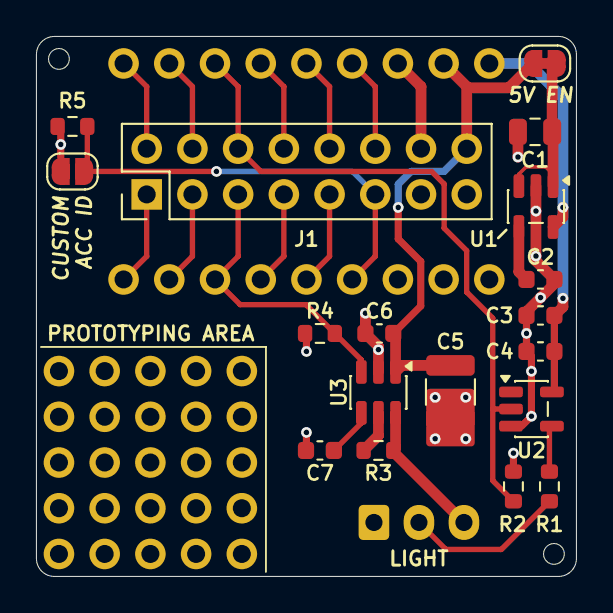
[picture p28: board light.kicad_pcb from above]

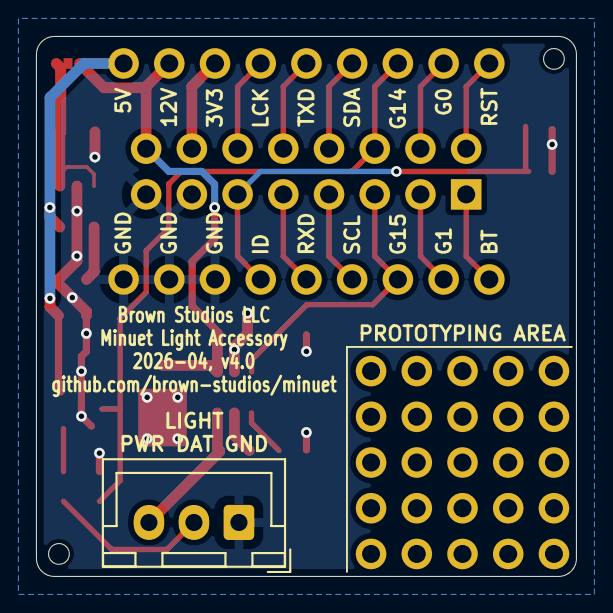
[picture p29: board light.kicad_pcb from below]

Board: 2 copper layers, 30.0 x 30.0 mm, 24 parts (3 on the bottom side), 23 nets.

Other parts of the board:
PROTO: Val**; ProtoPins
TH1, TH2: JLCPCB_PCBA_Tooling_Hole

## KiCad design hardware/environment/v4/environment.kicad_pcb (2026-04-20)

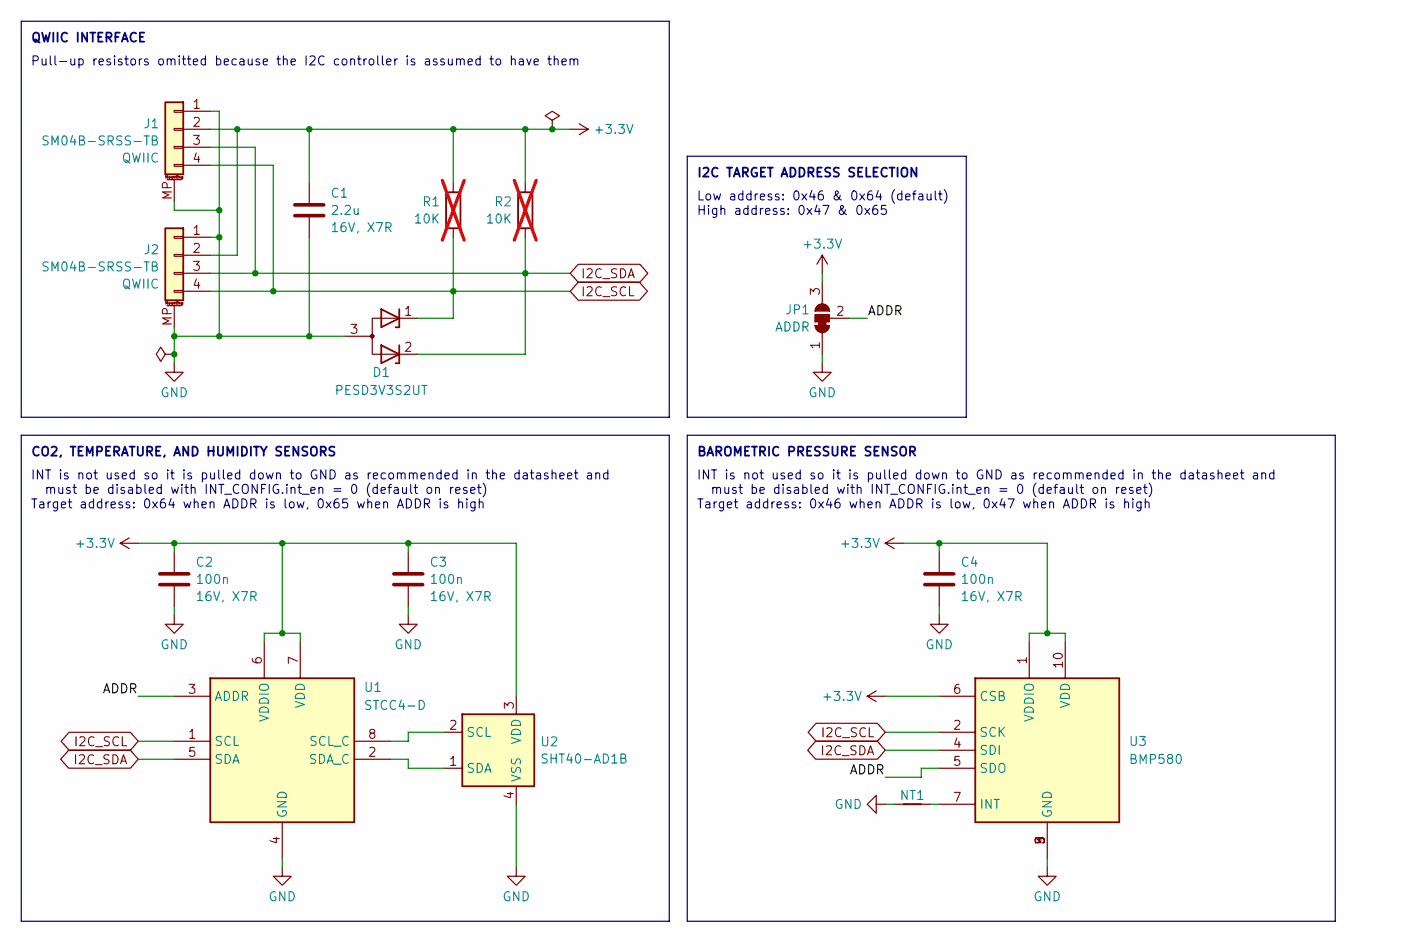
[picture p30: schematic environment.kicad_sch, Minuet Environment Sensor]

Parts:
C1: 2.2u; C_0805_2012Metric; Rating 16V, X7R; MPN CL21B225KOFNNNE; LCSC C28234
C2, C3, C4: 100n; C_0402_1005Metric; Rating 16V, X7R; MPN CL05B104KO5NNNC; LCSC C1525
D1: PESD3V3S2UT; SOT-23; LCSC C84276
J1, J2: SM04B-SRSS-TB; JST_SH_SM04B-SRSS-TB_1x04-1MP_P1.00mm_Horizontal; LCSC C160404
JP1: SolderJumper_3_Bridged12; SolderJumper-3_P1.3mm_Bridged12_RoundedPad1.0x1.5mm
NT1: NetTie_2; NetTie-2_SMD_Pad0.2mm
R1, R2: 10K; R_0402_1005Metric; Rating 1%; LCSC C25744; not fitted
U1: STCC4-D; STCC4; LCSC C49191471
U2: SHT40-AD1B; Sensirion_DFN-4_1.5x1.5mm_P0.8mm_SHT4x_NoCentralPad; LCSC C2848306
U3: BMP580; BMP581; LCSC C22391138

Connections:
+3.3V: C1.1, C2.1, C3.1, C4.1, J1.2, J2.2, JP1.3 (B), R1.1, R2.1, U1.6 (VDDIO), U1.7 (VDD), U2.3 (VDD), U3.1 (VDDIO), U3.6 (CSB), U3.10 (VDD)
/ADDR: JP1.2 (C), U1.3 (ADDR), U3.5 (SDO)
GND: C1.2, C2.2, C3.2, C4.2, D1.3 (A), J1.1, J1.MP (MountPin), J2.1, J2.MP (MountPin), JP1.1 (A), NT1.1, U1.4 (GND), U2.4 (VSS), U3.3 (GND), U3.8 (GND), U3.9 (GND)
I2C_SCL: D1.1 (K), J1.4, J2.4, R1.2, U1.1 (SCL), U3.2 (SCK)
I2C_SDA: D1.2 (K), J1.3, J2.3, R2.2, U1.5 (SDA), U3.4 (SDI)
unnamed: U1.8 (SCL_C), U2.2 (SCL)
unnamed: U1.2 (SDA_C), U2.1 (SDA)
unnamed: NT1.2, U3.7 (INT)

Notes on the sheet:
INT is not used so it is pulled down to GND as recommended in the datasheet and must be disabled with INT_CONFIG.int_en = 0 (default on reset) Target address: 0x64 when ADDR is low, 0x65 when ADDR is high
Pull-up resistors omitted because the I2C controller is assumed to have them
QWIIC INTERFACE
Low address: 0x46 & 0x64 (default) High address: 0x47 & 0x65
BAROMETRIC PRESSURE SENSOR
CO2, TEMPERATURE, AND HUMIDITY SENSORS
I2C TARGET ADDRESS SELECTION
INT is not used so it is pulled down to GND as recommended in the datasheet and must be disabled with INT_CONFIG.int_en = 0 (default on reset) Target address: 0x46 when ADDR is low, 0x47 when ADDR is high

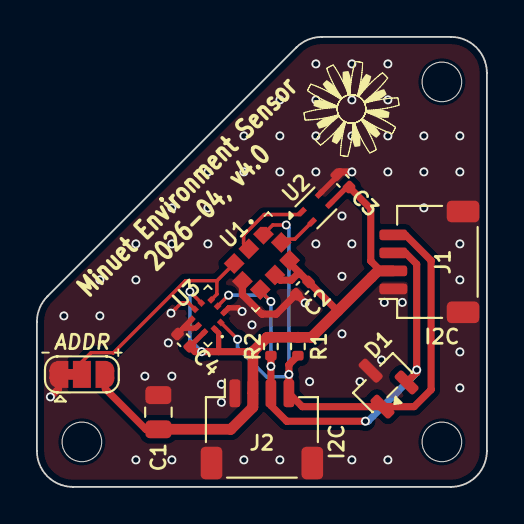
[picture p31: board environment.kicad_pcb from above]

Board: 4 copper layers, 25.0 x 25.0 mm, 17 parts (0 on the bottom side), 8 nets.

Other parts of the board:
H1, H1#2, H1#3: MountingHole_2.2mm_M2

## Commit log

2025-01-09 Add v1 hardware.
    [core.kicad_sch, fan.kicad_sch, keypad.kicad_sch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]
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2025-02-05 Work in progress on Minuet revision 2.
    This new revision uses a higher current BLDC driver for the fan motor
    and adds many features that were omitted from the initial prototype.
    [core.kicad_sch, cover.kicad_sch, fan.kicad_sch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]
2025-02-08 Complete draft of the v2 PCB
    [core.kicad_sch, cover.kicad_sch, fan.kicad_sch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]
2025-02-09 Create an accessory for driving lighting and other loads.
    Plugs into the Minuet v2 extension port.
    [driver.kicad_sch, load.kicad_pcb, load.kicad_sch]
2025-02-09 Prepare Minuet v2 for fabrication.
    [core.kicad_sch, fan.kicad_sch, minuet.kicad_pcb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]
2025-02-09 Move Minuet main board to a subdirectory.
    [core.kicad_sch, cover.kicad_sch, fan.kicad_sch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]
2025-02-09 Wordsmithing accessories and components.
    [core.kicad_sch, load.kicad_sch, minuet.kicad_sch]
2025-02-09 Finishing touches for v2
    [load.kicad_pcb]
2025-02-09 Finishing touches for v2.
    [minuet.kicad_pcb]
2025-02-20 Make the piezo buzzer symbol unpolarized.
    [minuet.kicad_sch]
2025-02-20 Update software and documentation for v2.
    Update all components to use the new I/O pins.
    Add IR receiver, piezo buzzer, wall control, rain sensor.
    Implement IR protocol parsing.
    Reorganize the YAML file by component.
    Update the motor docs with the v2 motor phase order.
    Rename the top-level configurations for clarity.
    Move secrets into their own file.
    The firmware is a work in progress, not all features are implemented.
    Worked around some errata to address in the next hardware revision.
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2025-02-20 Abandon load accessory design, update errata.
    Decided to abandon this design because it is overly complex and
    doesn't work with addressable LEDs as intended. It would be better
    to design simpler boards for each use-case instead of having lots
    of jumpers.
    [driver.kicad_sch, load.kicad_pcb, load.kicad_sch]
2025-02-21 Add new light accessory.
    Connects a dimmable LED or addressable LED strip to the fan.
    This design supersedes the prior lighting and load accessory and has
    been simplified for just this purpose.
    [light.kicad_pcb, light.kicad_sch]
2025-02-24 Replace maximum current with available current
2025-02-24 Finalize light accessory v2.5 for manufacture.
    [light.kicad_pcb, light.kicad_sch]
2025-02-24 Finalize Minuet v2.1 for manufacture.
    This revision uses a different motor controller and buck converter
    and remedies errata from v2.0.
    [core.kicad_sch, cover.kicad_sch, fan.kicad_sch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]
2025-03-10 Update Minuet v2.2 ILIM resistor setting.
    The default current limits are just a little too low, fix that in
    the next revision. Also improved the documentation with markdown tables
    for each setting.
    [fan.kicad_sch, minuet.kicad_sch]
2025-03-10 Redesign the control scheme and document it.
    Add an option to toggle between "standard" and "enhanced" controls
    which mainly changes how the automatic thermostat is configured
    using the keypad. The keypad behavior with the enhanced controls is
    modeless so the buttons always do the same thing regardless of whether
    the thermostat is on. The thermostat can be overridden just by pressing
    a button to change the state of the fan and then it can be re-engaged
    by pressing the auto button again. The user guide explains everything.
    Rewrote keypad decoding to support chorded keypresses and to immediately
    dispatch actions when buttons are held long enough instead of waiting
    for them to be released f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
2025-03-10 Increase motor PWM frequency and make it configurable for testing.
    Anything above about 20 KHz should render the switching noise inaudible
    to most people and higher frequencies incur greater switching losses.
    Set it to 24 KHz somewhat arbitrarily as that corresponds to the Nyquist
    frequency of CD quality audio recordings. Noted the difference with
    a spectrometer.
2025-03-10 Turn off motors and lights on shutdown.
    They'll be turned off when the hardware reinitializes after
    a reboot but it's better to be safe just in case.
2025-03-10 Support brushed fan motors on the MCT8316Z.
    This is a bit of a hack because it requires resetting the motor lock
    timeout periodically but it's enough to compare the behavior of the
    motors. The SPI variant of this chip allows the lock timeout to be
    disabled. Too bad it isn't I2C as that would be easier to work with.
    For the factory motor, connect the white wire to motor phase U and
    the black wire to motor phase V with a JST VH-3 connector. Also
    connect the hall V sensor to ground (wire pin 3 to pin 1 of the
    JST XH-5 connector).
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2025-04-14 Update the motor duty cycle table for the 50 W motor.
    This table should perhaps be replaced with some kind of speed control
    loop based on the tachometer reading.
2025-04-14 Improve lighting transitions.
    Disabled gamma correction for the addressable LED strips to workaround a
    problem with the fade in from off to on essentially doing nothing for
    the majority of the transition then jumping to the final state.
    See: https://github.com/esphome/issues/issues/2397
2025-04-14 Don't override auto fan control when direction changes and is same as manual
2025-04-14 Raise the arbitrary speed used for auto fan control.
    Still need to implement a control loop that accounts for temperature
    differences and human comfort.
2025-04-14 Set the wifi switch default to off for captive portals.
    Improves security when the user hasn't configured any credentials.
2025-04-21 Add a setting to override the fan duty cycle for testing purposes.
2025-04-21 Delay changing cover motor direction to prevent early stalls.
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2025-04-22 Snapshot both fan and cover on manual override.
    Ensures that the manually overridden state is preserved when the
    thermostat is disabled.
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2025-05-19 Duplicate v2 to begin work on v3.
    [core.kicad_sch, cover.kicad_sch, fan.kicad_sch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]
2025-05-22 First draft of Minuet v3.
    [core.kicad_sch, fan.kicad_sch, keypad.kicad_sch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]
2025-05-23 Prepare for fabrication.
    [core.kicad_sch, fan.kicad_sch, keypad.kicad_sch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]
2025-05-23 Move light accessory to v2.
    [light.kicad_pcb, light.kicad_sch]
2025-05-23 Create v3 of light accessory for redesigned expansion port.
    [light.kicad_pcb, light.kicad_sch]
2025-05-23 Remove unnecessary fields.
    [core.kicad_sch, fan.kicad_sch, keypad.kicad_sch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]
2025-06-05 Add a connector for input controls.
    [light.kicad_pcb, light.kicad_sch]
2025-06-06 Finalize light accessory for fabrication.
    [light.kicad_pcb, light.kicad_sch]
2025-06-06 Add support for 24 key infrared light remote.
    Improved color calibration and effects.
2025-06-06 Add tooling holes and PCBA offsets.
    [light.kicad_pcb, light.kicad_sch]
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2025-07-04 Prepare light accessory v3 for production
    [light.kicad_pcb, light.kicad_sch]
2025-07-04 Prepare Minuet v3 for production.
    [core.kicad_sch, fan.kicad_sch, keypad.kicad_sch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]
2025-07-10 Don't auto-reboot when the API connection is lost.
    The fan should always be capable of operating standalone.
2025-07-10 Emphasize dressing the wires to prevent damage during installation
2025-07-10 Improve auto and light controls.
    Add documentation on using a 24-key RGBW LED IR remote.
    Support changing the brightness of the light.
    Hold auto to reset the temperature setpoint in both modes.
    Fix a bug that would improperly exit auto when releasing a combo.
2025-07-11 Rewrite the logic for persisting fan state.
    Ensure that the state is restored correctly after a restart including
    whether the manual override has been engaged.
    The fan always turns off when the thermostat is disabled.
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2025-08-20 Fix sensor delta filters.
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2025-08-20 Add a diagnostic switch to engage the fan motor brake input.
    Useful for testing purposes. It has uncovered a possible conflict
    between the brake function and the watchdog timer that results in a
    WATCHDOG_FAULT being reported when braking.
2025-08-20 Handle motor driver sleep/wake behavior and faults.
    Allows time for transient faults to resolve themselves before stopping
    the motor..
2025-08-20 Revert to ESP-IDF 5.3.2 to workaround I2C errors in 5.4.2.
2025-08-21 Refactor fan driver code to shorten the identifiers a bit.
2025-08-23 Implement a simple automatic fan speed algorithm.
    Also added a few more thermostat presets.
2025-08-25 Use include vars for hardware compatibility.
    Updated core.yaml to support Minuet v3.0 and v3.1 pin differences.
    Updated light accessories to support various LED strips.
    Added errata and workaround regarding GPIO6 pin initial state in v3.0.
2025-08-25 Add step files for making assembly fixtures
    [light.step]
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2025-08-29 Add standoff model height to errata.
2025-08-29 Remove superseded hardware designs.
    They will remain in the git history for posterity.
    [core.kicad_sch, cover.kicad_sch, driver.kicad_sch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]
2025-09-12 Add direct links to each PCB design near the top of the hardware guide
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2025-09-22 Add a more informative table of compatible hardware.
    Amend errata with the limitations of the current end-of-travel detection
    method for the lid motor.
2025-09-22 Add a wire passage cover model and improved the installation instructions.
    Also updated the link for the fan motor mount model.
2025-09-22 Fix the JST VH connector housing designation for the motor
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2025-09-28 Clarify the type of screw to use for the motor mount adapter.
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2025-10-26 Migrate light project to KiCad 9 for v4.
    [light.kicad_pcb, light.kicad_sch]
2025-10-26 Migrate minuet project to KiCad 9 for v4.
    [core.kicad_sch, fan.kicad_sch, keypad.kicad_sch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]
2026-02-25 Wordsmithing and link to firmware repo.
    [light.kicad_sch]
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2026-04-04 First draft of Minuet v4 fan controller board
    [core.kicad_sch, fan.kicad_sch, keypad.kicad_sch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]
2026-04-10 Second draft of Minuet v4 main board.
    [core.kicad_sch, fan.kicad_sch, keypad.kicad_sch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]
2026-04-10 First draft of Minuet light accessory v4.
    [light.kicad_pcb, light.kicad_sch]
2026-04-13 Add DNP footprint for CT slew rate capacitor.
    [light.kicad_pcb, light.kicad_sch]
2026-04-13 Move IR receiver to center on aperture
    [minuet.kicad_pcb]
2026-04-20 Design environment sensor.
    [environment.kicad_pcb, environment.kicad_sch]
2026-04-20 Prepare light accessory for fabrication
    [light.kicad_pcb]
2026-04-21 Prepare main board for fabrication
    [fan.kicad_sch, keypad.kicad_sch, lid.kicad_sch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]
